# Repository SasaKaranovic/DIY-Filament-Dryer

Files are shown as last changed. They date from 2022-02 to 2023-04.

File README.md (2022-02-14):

# DIY WiFi Enabled 3D Printing Filament Dry Box

## What is this project about?
DIY WiFi Enabled Filament Dry Box (http://www.youtube.com/watch?v=txF2oQPIjb4 "DIY WiFi Enabled Filament Dry Box")

Above video shows the finished DryBox, how it works and motivation behind some of the design decisions.

## How can I build my own?
The above video explains the idea and how hardware and firmware works. It's recommended that you watch that first.
Hardware and firmware build instructions and source files are available in their respective folders.

---

Blog page: https://sasakaranovic.com/projects/diy-filament-dry-box

YouTube video: http://www.youtube.com/watch?v=txF2oQPIjb4

---

#### Sasa Karanovic

<a href="https://sasakaranovic.com/" target="_blank" title="Sasa Karanovic Home Page"> Home Page</a> &nbsp;&middot;&nbsp;
<a href="https://youtube.com/c/sasakaranovic" target="_blank" title="Sasa Karanovic on YouTube"> YouTube</a> &nbsp;&middot;&nbsp;
<a href="https://github.com/sasakaranovic" target="_blank" title="Sasa Karanovic on GitHub"> GitHub</a> &nbsp;&middot;&nbsp;
<a href="https://twitter.com/_sasakaranovic_" target="_blank" title="Sasa Karanovic on Twitter"> Twitter</a> &nbsp;&middot;&nbsp;
<a href="https://instagram.com/_sasakaranovic_" target="_blank" title="Sasa Karanovic on Instagram"> Instagram</a> &nbsp;&middot;&nbsp;
<a href="https://buymeacoffee.com/sasakaranovic" target="_blank" title="Sasa Karanovic on Buy me a coffee"> Buy me a coffee</a>

[home]: https://raw.githubusercontent.com/SasaKaranovic/common/master/assets/img_home.png "Sasa Karanovic Home Page"
[youtube]: https://raw.githubusercontent.com/SasaKaranovic/common/master/assets/img_youtube.png "Sasa Karanovic YouTube channel"
[github]: https://raw.githubusercontent.com/SasaKaranovic/common/master/assets/img_github.png "Sasa Karanovic on GitHub"
[twitter]: https://raw.githubusercontent.com/SasaKaranovic/common/master/assets/img_twitter.png "Sasa Karanovic on Twitter"
[instagram]: https://raw.githubusercontent.com/SasaKaranovic/common/master/assets/img_instagram.png "Sasa Karanovic on Instagram"
[coffee]: https://raw.githubusercontent.com/SasaKaranovic/common/master/assets/img_coffee.png "Buy me a coffee"

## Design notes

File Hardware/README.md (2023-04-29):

# Building the Hardware

### Schematic
Schematic files are available in `Schematic.pdf` as well as Altium source files.
This file should be enough to understand how things are connected and how hardware works.

Bill of Material is available in `Bill of Materials.pdf`.
Most parts are interchangeable, so feel free to source these parts from your favorite part distributor.
When replacing capacitors, make sure you choose the same voltage rating!

### How can I order the PCB

I have prepared Gerber files that are verified and ready to go. You can take `Release\2023-04-29_14-32_DryBox_R1\2023-04-29_14-32_DryBox_R1_Gerber.zip` and upload it to your favorite PCB manufactuer like PCBWay, SeeedStudio, JLCPCB etc.
There are no critical PCB specs, so you can select whichever one you prefer.
For your reference, the specifications for the PCBs that I have ordered are listed below.

PCB Specs:
- Board type: Single pieces
- Different Design in Panel：1
- Layer: 2 Layers
- Thickness: 1.6 mm
- Min Track/Spacing: 6/6mil
- Material: FR-4: TG150
- Min Hole Size: 0.3mm ↑
- Solder Mask: White
- Silkscreen: Black
- Quantity: 10 (or however many you need)
- Edge connector: No
- Surface Finish: HASL lead free (or ENIG but it's more expensive)
- "HASL" to "ENIG"  Yes
- Via Process: Tenting vias
- Finished Copper: 1 oz Cu

## Changelog

### 2023-04-29

- Corrected U3 part number

### 2021-12-07

- Initial release

[<- Go back to repository root](../README.md)

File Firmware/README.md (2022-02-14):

# How to build firmware

For our firmware development, we are going to use Arduino. Mainly because it's user friendly, easy to use and
most hobbyists are familiar with it or have already used it. While we could build te same or even more efficient
firmware using C and ESP-IDF, we are going to stick with Arduino and hope that this allows the project to be
more friendly and easier to use/modify by wider DIY/hacker community.

## How can I build/compile firmware?
Arduino has many third party libraries that you can use and also build firmware for many different boards.
However, depending for which board you are building firmware and also which libraries your project (sketch) uses,
you might need to manually install them or download them trough board/library manager.

While above mentioned solution works fine, it can lead to issues like installing the "wrong/different" version
of the library, different board files, "wrong/different" build/upload tools and so on. On top of that, since board files
and libraries are shared, we could install a library or a board file while working on another project that breaks our current project.
Hopefully you can see why this is not so great for open-source open-hardware project where we want everyone to be able to easily
checkout a repository and hit the ground running without spending hours setting up and debugging what library or board files are missing.

Luckily we can automate/avoid this by using a build system like PlatformIO. So below we will have two ways of building
the firmware, one will be "easy" by leveraging PlatformiIO build system, and the other one will be a manual one by using
Arduino IDE and manually searching and downloading all the board/library files.

## - The super easy way - Compile and upload using PlatformIO build system  - 

### 1. Install PlatformIO
Installing PlatformIO CLI is pretty straight-forward and also well documented for Windows, Linux and MacOS.
You will need to follow few steps and get PlatformIO CLI installed, detailed tutorial can be found at https://platformio.org/install/cli
Make sure to install [PlatformIO Core](https://docs.platformio.org/en/latest//core/installation.html#installation-methods 'https://docs.platformio.org/en/latest//core/installation.html#installation-methods') and allso that it is available trough [shell](https://docs.platformio.org/en/latest//core/installation.html#piocore-install-shell-commands 'PlatformIO Core - Install Shell Commands¶').

### 2. Build firmware
Open shell/command-prompt and navigate to 'Firmware/platformio' folder.
1. Compile the firmware by typing `pio run`, PlatformIO will download all the required board files and libraries and finally compile the firmware.
2. Upload the firmware with `pio run --target upload --upload-port <COM-PORT>`. Make sure to replace `<COM-PORT>` with your ESP32's COM port (ie COM1 or /dev/ttyACM0)
3. Upload the file system (Web page) with `pio run --target uploadfs --upload-port <COM-PORT>`, again replace `<COM-PORT>` with your ESP32's COM port.

Every time you make a firmware change, you need to run steps #1 and #2.
Every time you make a change to the web page (anything inside `data` folder) you only need to run step #3.

## - The less easy way - Compile using Arduino IDE and manually install all board files and libraries

### 1. Install Arduino IDE
Download and install Arduino IDE from https://www.arduino.cc/en/software

### 2. Install ESP32 board files
Add ESP32 board files to you Arduino IDE
1. Go to `File -> Preferences`
2. Find `Additional Board Manager URLs:` and add `https://dl.espressif.com/dl/package_esp32_index.json`
3. Go to `Boards -> Board manager`.
4. Search for `esp32`.
5. Find a board package title `esp32 -> by Espressif Systems` and install it.
(Currently we are using version 1.0.6, in case you have any issues, try installing this exact version)

### 3. Install libraries used by the project
Install third party libraries that required
1. Go to `Sketch -> Include Library -> Manage Libraries... (CTRL+SHIFT+I)`
2. Find libraries from the list below and install them one by one

- Adafruit SHT31 Library (version 2.0.0)
- Adafruit Si7021 Library (version 1.5.0)
- DallasTemperature (version 3.9.0)
- OneWire (version 2.3.6)

### 4. Install some more libraries
You will manually have to install following libraries.
One way is to create a `Libraries` folder in your sketch folder. Then download the libraries and place them in Libraries folder.

- https://github.com/me-no-dev/AsyncTCP
- https://github.com/me-no-dev/ESPAsyncWebServer

### 5. Select build board
You need to tell Arduino IDE for which board we want to build the firmware.
Go to `Tools -> Board: -> ESP32 Arduino` and select `ESP32 Dev Module`
Go to `Tools -> Port` and select your ESP32 COM port

### 6. Compile and upload the firmware
You need to compile and upload firmware.
Go to `Sketch -> Upload`
You will need to do this step every time you make a change to the firmware.

### 7. Upload the file system
You need to tell Arduino IDE which partition scheme we want to use
Go to `Tools -> Partition Scheme` and select `1MB APP / 3MB SPIFF`
Now you can go upload file system trough `Tools -> ESP32 Sketch Data Upload` menu item.
If you are missing above menu item, you will need to manually install [ESP32 Sketch Data Upload tool](https://github.com/me-no-dev/arduino-esp32fs-plugin).
You will need to do this step every time you make a change to the web page (or anything inside the data folder)

[<- Go back to repository root](../README.md)

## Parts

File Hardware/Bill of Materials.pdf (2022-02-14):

Designator | Description | Distributor | Distributor Part Number | Manufacturer | Manufacturer Part Number | Quantity
C1, C6, C15, C22 | Capacitor | DigiKey | 1276-1870-1-ND | Samsung Electro-Mechanics | CL10A106MO8NQNC | 4
C2, C4, C8, C9, C11, C13, C14, C21 | Capacitor | DigiKey | 1276-1009-1-ND | Samsung Electro-Mechanics | CL10B103KB8NNNC | 8
C3, C10 | Polarized Capacitor (Axial) | DigiKey | 732-9599-1-ND | Würth Elektronik | 860160674021 | 2
C5, C7, C12, C20 | Capacitor | DigiKey | 1276-1860-1-ND | Samsung Electro-Mechanics | CL10A105KB8NNNC | 4
D1 | Red, Green, Blue (RGB) - LED Indication - Discrete 1.9V Red, 2.8V Green, 2.8V Blue 0606 (1616 Metric) | DigiKey | 1080-1551-1-ND | Everlight Electronics Co Ltd | EAST1616RGBB2 | 1
D2, D3, D4 | | DigiKey | 1727-3848-1-ND | Nexperia USA Inc. | PMEG6010CEH,115 | 3
F1 | Thermal Fuse | DigiKey | SF-1206SP200-2CT-ND | Bourns Inc. | SF-1206SP200-2 | 1
L1 | Inductor | DigiKey | 445-180842-1-ND | TDK Corporation | VLS6045AF-101M | 1
P1, P2, P3, P4, P5, P8, P11 | Header, 4-Pin, Header, 3-Pin, Dual row, Header, 2-Pin, Header, 3-Pin | | | | | 7
Q1, Q3 | MOSFET N-CH 60V 0.38A | DigiKey | DMN62D0U-13DICT-ND | Diodes Incorporated | DMN62D0U-13 | 2
Q2 | MOSFET N-CH 30V 37A LFPAK | DigiKey | | Nexperia USA Inc. | PSMN011-30YLC,115 | 1
R1, R11 | Resistor | DigiKey | RMCF0603JT2K20CT-ND | Stackpole Electronics Inc | RMCF0603JT2K20 | 2
R2, R3, R10 | Resistor | DigiKey | RMCF0603FT220RCT-ND | Stackpole Electronics Inc | RMCF0603FT220R | 3
R5, R18, R23 | Resistor | DigiKey | RMCF0603JT10K0CT-ND | Stackpole Electronics Inc | RMCF0603JT10K0 | 3
R6, R7, R8, R9, R12 | Resistor | DigiKey | RMCF0603FT4K70CT-ND | Stackpole Electronics Inc | RMCF0603FT4K70 | 5
R13, R17, R22 | Resistor | DigiKey | RMCF0603FT100RCT-ND | Stackpole Electronics Inc | RMCF0603FT100R | 3
R19 | Resistor | DigiKey | RNCS0603BKE1K00CT-ND | Stackpole Electronics Inc | RNCS0603BKE1K00 | 1
R20 | Resistor | DigiKey | RMCF0603ZT0R00CT-ND | Stackpole Electronics Inc | RMCF0603ZT0R00 | 1
SW1 | SWITCH TACTILE SPST-NO 0.05A 12V | DigiKey | CKN9088CT-ND | C&K | PTS645SL50SMTR92 LFS | 1
U1 | | | | Espressif Systems | ESP32-WROOM-32D (4MB HIGH TEMP) | 1
U2 | Switching mode regulator [ 3v3, 5v, 12v and ADJ ] | DigiKey | LM2576S-5.0/NOPB-ND | Texas Instruments | LM2576S-5.0/NOPB | 1
U3 | High-Performance Single 1.8V@150mA LDO | DigiKey | 576-4082-1-ND | Microchip Technology | MIC5365-1.8YD5-TR | 1

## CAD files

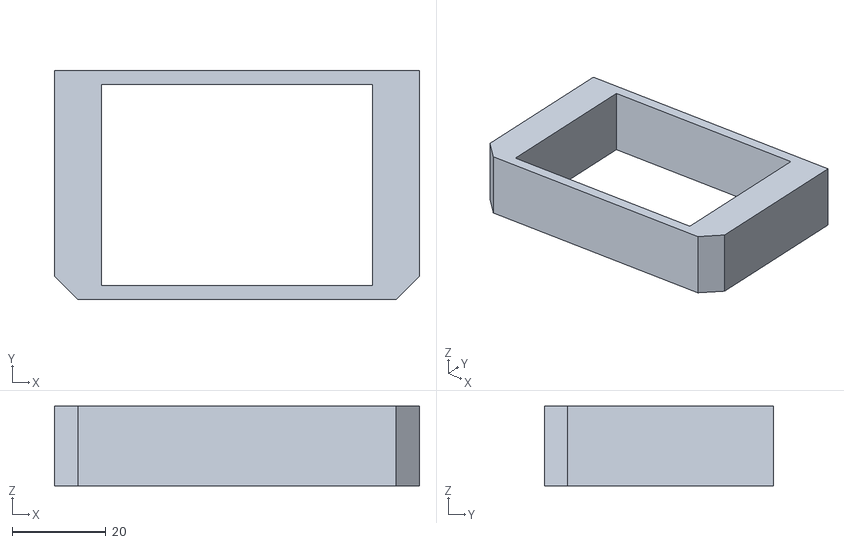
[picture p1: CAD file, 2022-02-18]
3D_Parts/Rubber_Friction_Mount_TPU.stl
78.0 x 49.0 x 17.0

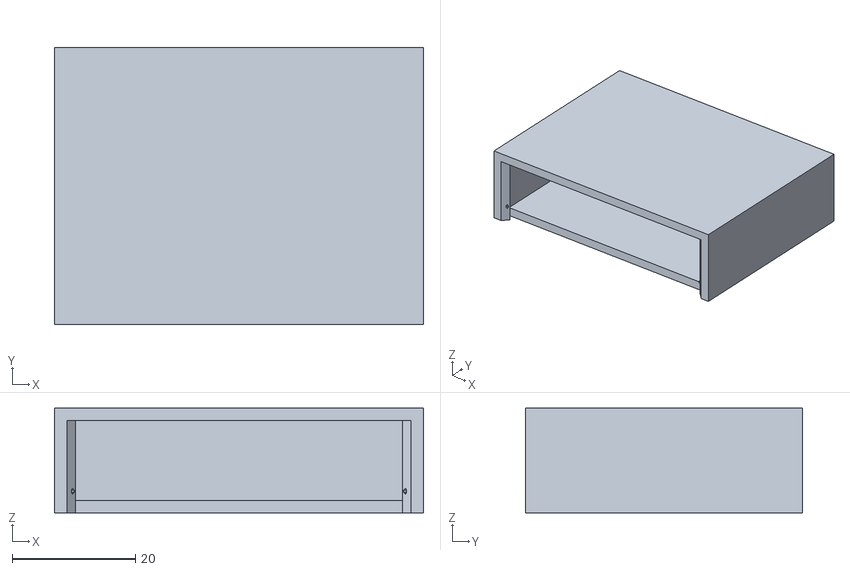
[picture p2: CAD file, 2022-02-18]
3D_Parts/Desiccant_Holder_PLA_or_PETG.stl
60.0 x 45.0 x 17.0

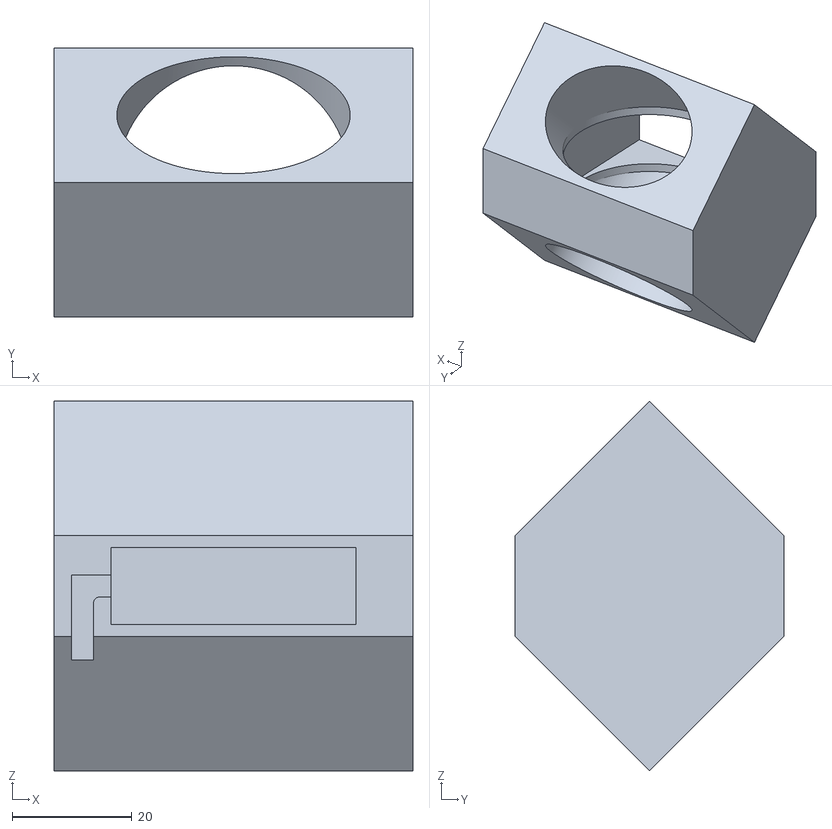
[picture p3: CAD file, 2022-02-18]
3D_Parts/FanHolder_PLA_or_PETG.stl
60.0 x 45.0 x 61.8

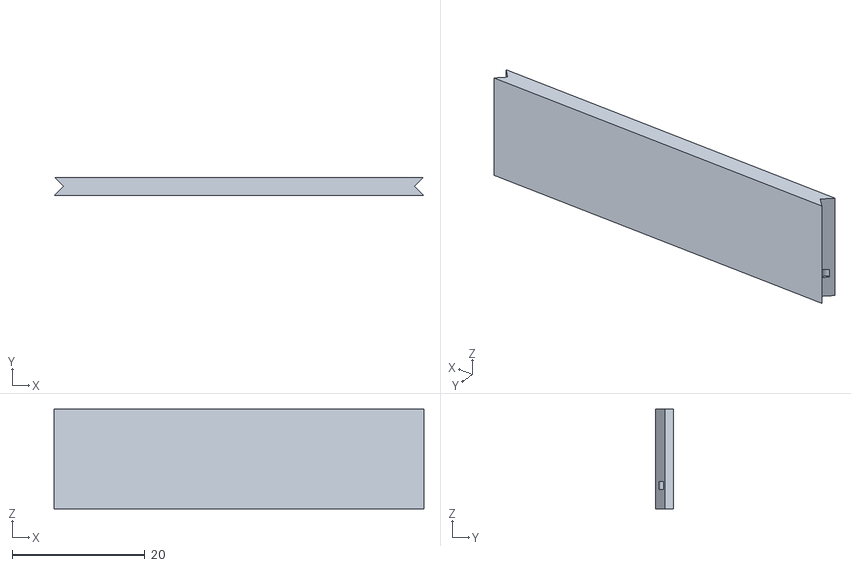
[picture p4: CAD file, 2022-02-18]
3D_Parts/Desiccant_Cap_PLA_or_PETG.stl
55.7 x 2.73 x 15.0

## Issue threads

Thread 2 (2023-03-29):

BOM Parts.

SilentStray, 2023-03-29:
Header Part Numbers:
P2 | Connector   Header Through Hole 6 position 0.100" (2.54mm) | DigiKey | S2011EC-03-ND | Sullins   Connector Solutions | PRPC003DAAN-RC | Quantity - 1

P3,P8 | Connector   Header Through Hole 2 position 0.100" (2.54mm) | DigiKey | S1011EC-02-ND | Sullins   Connector Solutions | PRPC002SAAN-RC | Quantity - 2

P1,P4,P11 | Connector   Header Through Hole 4 position 0.100" (2.54mm) | DigiKey | S1011EC-04-ND | Sullins   Connector Solutions | PRPC004SAAN-RC | Quantity - 3

P5 | Connector   Header Through Hole 3 position 0.100" (2.54mm) | DigiKey | S1011EC-03-ND | Sullins   Connector Solutions | PRPC003SAAN-RC | Quantity - 1

L1 is out of stock on DigiKey:

L1 | Inductor | Mouser | 810-VLS6045AF-101M | TDK Corporation | VLS6045AF-101M |  Quantity - 1

SilentStray, 2023-03-30:
Made a pull request.

Closed 2023-03-30.

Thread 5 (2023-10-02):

PID values when 'Using HEATER as target temperature' returning negative

benuron, 2023-10-02:
Hi Sasa, thanks for sharing this project and make it available to everyone :)

I am trying to setup the whole project since a while now, I am not a code expert so my efforts to fix some bugs are reaching a limit.

One situation that is that when the max_heater_temperature reaches the set value the PID values starts to get negative and the calculated PWM values shoot to the max and the heater keeps ON.

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

Am I missing something?
I am trying to create a branch and contribute for this project as soon as I understand git better 👍

SasaKaranovic, 2024-02-29:
@benuron appologies for late reply. I somehow missed that you have opened this issue.

Did you modify the code or using it as-is?

I am working on a new version of this project that should hopefully be better and offer some quality of life improvements.

benuron, 2024-03-03:
@SasaKaranovic thanks for replying!

I am using some slightly modified code but nothing regarding the PID. In my code I changed the wifi connection, and I am using two SHT31 ```
Adafruit_SHT31 temp_sensor_in = Adafruit_SHT31();
Adafruit_Si7021 temp_sensor_out = Adafruit_SHT31();
```
and in this section I modified the i2c address in the temp_sensor_out

```
 // Setup temperature and humidity oneWireSensors
    if (!temp_sensor_out.begin(0x45))
    {
        Serial.println("Can't find Si7021 sensor! (out sensor)");
        LED_ALL_OFF();
        while (1)
        {
            LED_ON(PIN_LED_BLUE);
            delay(250);
            LED_OFF(PIN_LED_BLUE);
            delay(250);
        }
    }

    Wire.setClock(10000);
    if (!temp_sensor_in.begin(0x44))
    {
        Serial.println("Can't find SHT31! (in sensor)");
        LED_ALL_OFF();
        while (1)
        {
            LED_ON(PIN_LED_GREEN);
            delay(250);
            LED_OFF(PIN_LED_GREEN);
            delay(250);
        }
    }   if (!temp_sensor_out.begin())
    {
        Serial.println("Can't find Si7021 sensor! (out sensor)");
        LED_ALL_OFF();
        while (1)
        {
            LED_ON(PIN_LED_BLUE);
            delay(250);
            LED_OFF(PIN_LED_BLUE);
            delay(250);
        }
    }

    Wire.setClock(10000);
    if (!temp_sensor_in.begin(0x44))
    {
        Serial.println("Can't find SHT31! (in sensor)");
        LED_ALL_OFF();
        while (1)
        {
            LED_ON(PIN_LED_GREEN);
            delay(250);
            LED_OFF(PIN_LED_GREEN);
            delay(250);
        }
    }
```
From the webUI, all values are good, just the strange behaviour with the PID. I tried to manually tweak them a bit but without much success. Would be possible to have a PID autotune feature like in Marlin firmware?

There is a difference in hardware from my S1 (I have five) to yours. They all run with 24V power supplies. With the BOM for 12V the MOSFET generates a bunch of heat. I had to recalculate the voltage divider values so the MOSFET is full on/off.

Would love to try the new version, thank you for the efforts!

SasaKaranovic, 2024-06-05:
Closing due to inactivity. We can pick it up if new information becomes available.

razserv2010, 2024-08-01:
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

Hi SasaKaranovic
Is there already a new version?

Closed 2024-06-05.

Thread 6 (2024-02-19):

A fatal error occurred: Failed to connect to ESP32: No serial data received.

razserv2010, 2024-02-19:
I'm experiencing a error:
A fatal error occurred: Failed to connect to ESP32: No serial data received.
I connected using FTDI232
3V3 - 3V3
TX - RX
RX - TX
GND - GND

Could it be that the U3 component is MIC5365-1.8YD5-TR instead of 3V3?

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

SasaKaranovic, 2024-02-19:
Hi Raz,

Sorry about that, there was a typo in the BoM but it's fixed now.
You would need `MIC5365-3.3YD5-TR` (or any other equivalent 3v3 LDO).

razserv2010, 2024-02-19:
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

So this is the reason why the pc does not recognize the esp32?

SasaKaranovic, 2024-02-19:
Yes. The regulator you are using is providing ESP32 with 1.8V which is not enough for it to power up.
If you switch to a 3.3V regulator, it should work (assuming everything else is ok).

razserv2010, 2024-02-19:
> Yes. The regulator you are using is providing ESP32 with 1.8V which is not enough for it to power up.
> If you switch to a 3.3V regulator, it should work (assuming everything else is ok).

Thanks, I ordered 3v

SasaKaranovic, 2024-02-19:
Sorry about that. The release files and the Altium files were updated a long time ago but when you mentioned it, I realized that the schematic is still calling out the wrong LDO.

razserv2010, 2024-02-19:
> Sorry about that. The release files and the Altium files were updated a long time ago but when you mentioned it, I realized that the schematic is still calling out the wrong LDO.

Sorry but I didn't understand, LDO?

SasaKaranovic, 2024-02-20:
[LDO regulator](https://en.wikipedia.org/wiki/Low-dropout_regulator).
The schematic had the wrong LDO part number. If you replace it with 3.3V regulator, it should work.

razserv2010, 2024-02-20:
> [LDO regulator](https://en.wikipedia.org/wiki/Low-dropout_regulator).
> The schematic had the wrong LDO part number. If you replace it with 3.3V regulator, it should work.

Thanks, I ordered 3.3V

razserv2010, 2024-02-25:
> [LDO regulator](https://en.wikipedia.org/wiki/Low-dropout_regulator). The schematic had the wrong LDO part number. If you replace it with 3.3V regulator, it should work.

I replaced the component but still:
A fatal error occurred: Failed to connect to ESP32: No serial data received.

What is the order of UART connections? , maybe I didn't connect correctly..

razserv2010, 2024-02-26:
> [LDO regulator](https://en.wikipedia.org/wiki/Low-dropout_regulator).
> The schematic had the wrong LDO part number. If you replace it with 3.3V regulator, it should work.

 After I replaced the component, I was able to upload the firmware but the esp32 does not connect to wifi

razserv2010, 2024-02-26:
Until the Si7021 sensors arrive, I want to connect the board but it won't let me connect to wifi
How can Si7021 be bypassed?

katodo, 2024-02-27:
you can start to bypass "if (!temp_sensor_out.begin())" at the begin of code.

SasaKaranovic, 2024-02-29:
@razserv2010 As @katodo said you could stub out (comment out) parts of the code that rely on Si7021.
But it might be tedious and also I would recommend using the sensor since some portions of the code depend on it.

I am working on new version of this board that should offer some improvements that people have asked for.

razserv2010, 2024-03-01:
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

The sensors arrived, trying to connect to wifi but without success, I opened a new issue about it.

Closed 2024-03-02.

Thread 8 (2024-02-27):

(R4) component Also missing is the Bill of Materials

razserv2010, 2024-02-27:
I noticed that the R4 component is missing, Could you please provide the name of the component needed?
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

SasaKaranovic, 2024-02-29:
R4 is marked as DNP (do not populate or do not purchase). So you are correct not to populate it on the board.

This is a fallback if you are using an adjustable voltage regulator in which case you would change the value of R20 and R4.

Closed 2024-02-29.

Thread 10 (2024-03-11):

Custom Board: Can't connect to WiFi

razserv2010, 2024-03-11:
My board only manages to connect to wifi if the UART flasher is also connected, if I disconnect the UART and leave only the main power connected then the wifi does not connect.
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

SasaKaranovic, 2024-06-05:
Closing due to inactivity. We can pick it up if new information becomes available.

Closed 2024-06-05.

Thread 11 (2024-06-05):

errors in compile wiith platformio

Motarbio, 2024-06-05:
compiling aborted with this errors

> pio run
Processing esp32dev (framework: arduino; platform: espressif32; board: esp32dev)
---------------------------------------------------------------------------------------------------
Verbose mode can be enabled via `-v, --verbose` option
CONFIGURATION: https://docs.platformio.org/page/boards/espressif32/esp32dev.html
PLATFORM: Espressif 32 (6.7.0) > Espressif ESP32 Dev Module
HARDWARE: ESP32 240MHz, 320KB RAM, 4MB Flash
DEBUG: Current (cmsis-dap) External (cmsis-dap, esp-bridge, esp-prog, iot-bus-jtag, jlink, minimodule, olimex-arm-usb-ocd, olimex-arm-usb-ocd-h, olimex-arm-usb-tiny-h, olimex-jtag-tiny, tumpa)
PACKAGES:
 - framework-arduinoespressif32 @ 3.20016.0 (2.0.16)
 - tool-esptoolpy @ 1.40501.0 (4.5.1)
 - tool-openocd-esp32 @ 2.1100.20220706 (11.0)
 - toolchain-xtensa-esp32 @ 8.4.0+2021r2-patch5
Converting src.ino
LDF: Library Dependency Finder -> https://bit.ly/configure-pio-ldf
LDF Modes: Finder ~ chain, Compatibility ~ soft
Found 40 compatible libraries
Scanning dependencies...
Dependency Graph
|-- SPI @ 2.0.0
|-- SPIFFS @ 2.0.0
|-- FS @ 2.0.0
|-- WiFi @ 2.0.0
|-- Adafruit SHT31 Library @ 2.2.2
|-- Adafruit Si7021 Library @ 1.5.3
|-- ESP Async WebServer @ 1.2.3
|-- AsyncTCP @ 1.1.1
|-- DallasTemperature @ 3.11.0
|-- OneWire @ 2.3.8
|-- ESPmDNS @ 2.0.0
|-- Wire @ 2.0.0
Building in release mode
Compiling .pio\build\esp32dev\src\src.ino.cpp.o
Linking .pio\build\esp32dev\firmware.elf
c:/users/magut/.platformio/packages/toolchain-xtensa-esp32/bin/../lib/gcc/xtensa-esp32-elf/8.4.0/../../../../xtensa-esp32-elf/bin/ld.exe: .pio\build\esp32dev\lib0ed\libESP Async WebServer.a(WebAuthentication.cpp.o):(.literal._ZL6getMD5PhtPc+0x4): undefined reference to `mbedtls_md5_starts'
c:/users/magut/.platformio/packages/toolchain-xtensa-esp32/bin/../lib/gcc/xtensa-esp32-elf/8.4.0/../../../../xtensa-esp32-elf/bin/ld.exe: .pio\build\esp32dev\lib0ed\libESP Async WebServer.a(WebAuthentication.cpp.o): in function `getMD5(unsigned char*, unsigned short, char*)':
C:\Users\Magut\Downloads\DIY-Filament-Dryer-master\DIY-Filament-Dryer-master\Firmware\platformio/.pio/libdeps/esp32dev/ESP Async WebServer/src/WebAuthentication.cpp:73: undefined reference to `mbedtls_md5_starts'
collect2.exe: error: ld returned 1 exit status
*** [.pio\build\esp32dev\firmware.elf] Error 1

SasaKaranovic, 2024-06-05:
Hey @Motarbio

From the output it looks like PlatformIO is identifying conflict between libraries.

Can you try updating `platformio.ini` file and changing lines Line 29 and Line 30 (https://github.com/SasaKaranovic/DIY-Filament-Dryer/blob/master/Firmware/platformio/platformio.ini#L29-L30) to be as follows

```
    https://github.com/me-no-dev/ESPAsyncWebServer.git
    https://github.com/me-no-dev/AsyncTCP.git
```

Motarbio, 2024-06-05:
Hi Now the error is please install  git clientDegiorgi Tiziano Il giorno 4 giu 2024, alle ore 22:02, Sasa Karanovic ***@***.***> ha scritto:
Hey @Motarbio
From the output it looks like PlatformIO is identifying conflict between libraries.
Can you try updating platformio.ini file and changing lines Line 29 and Line 30 (https://github.com/SasaKaranovic/DIY-Filament-Dryer/blob/master/Firmware/platformio/platformio.ini#L29-L30) to be as follows
    https://github.com/me-no-dev/ESPAsyncWebServer.git
    https://github.com/me-no-dev/AsyncTCP.git

—Reply to this email directly, view it on GitHub, or unsubscribe.You are receiving this because you were mentioned.Message ID: ***@***.***>

SasaKaranovic, 2024-06-05:
@Motarbio Can you try doing that?
You can install a Git client from https://git-scm.com/download/win (assuming you use Windows)

Motarbio, 2024-06-05:
Done, nothing dame errorDegiorgi Tiziano Il giorno 4 giu 2024, alle ore 23:08, Sasa Karanovic ***@***.***> ha scritto:
@Motarbio Can you try doing that?
You can install a Git client from https://git-scm.com/download/win (assuming you use Windows)

—Reply to this email directly, view it on GitHub, or unsubscribe.You are receiving this because you were mentioned.Message ID: ***@***.***>

SasaKaranovic, 2024-06-05:
Please try restarting your computer after installing Git client and then try again.

p.s. When you reply via email, it messes up the formatting on the GitHub issue.

Motarbio, 2024-06-05:
pc restarted, same error
Library Manager: Installing git+https://github.com/me-no-dev/ESPAsyncWebServer.git
UserSideException: Please install Git client from https://git-scm.com/downloads

Motarbio, 2024-06-05:
Hi there,
downloaded manually the libraries, compiled succesfully but with 2 warnings

Library Manager: Installing ESPAsyncWebServer-master
Warning! Could not find the package with 'ESPAsyncWebServer-master' requirements for your system 'windows_amd64'
Library Manager: Installing AsyncTCP-master
Warning! Could not find the package with 'AsyncTCP-master' requirements for your system 'windows_amd64'

SasaKaranovic, 2024-06-06:
You should double check if `git` is in your system `PATH` variable. Then PlatformIO should be able to pull those libraries for you automatically.

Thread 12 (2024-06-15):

ignores heater temp limit

gabecamp, 2024-06-15:
seems to ignore the heater temp limit and goes to 100c ,built as normal except for using 2 Adafruit SHT31 as in and out sensors,

SasaKaranovic, 2024-06-15:
@gabecamp Is the heater sensor reporting that temperature or you manually measured it?
Can you share which components you used and which PCB vendor?

gabecamp, 2024-06-16:
Using all the parts from the BOM on GitHub except for 2 sh31 sensors , the PCBs were using the Gerber's from github with jlcpcb. The temps are from the ds18b20 as per the schematic.  After some testing I found it does hold temp correctly after turning it off and letting it cool a few times. Could it possibly be the pid loop causing thermal runaway?

SasaKaranovic, 2024-06-17:
It's good that it's stable now.
I had mine running for couple of years now and had no issues.
If you find way to reproduce this, please let me know.

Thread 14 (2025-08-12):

PlatformIO build: FAILED

wigw, 2025-08-12:
Добрий день.
Даруйте мені, я не можу скомпілювати прошивку, пише FAILED.
Що я роблю не так

[FAILED.txt](https://github.com/user-attachments/files/21729861/FAILED.txt)

?

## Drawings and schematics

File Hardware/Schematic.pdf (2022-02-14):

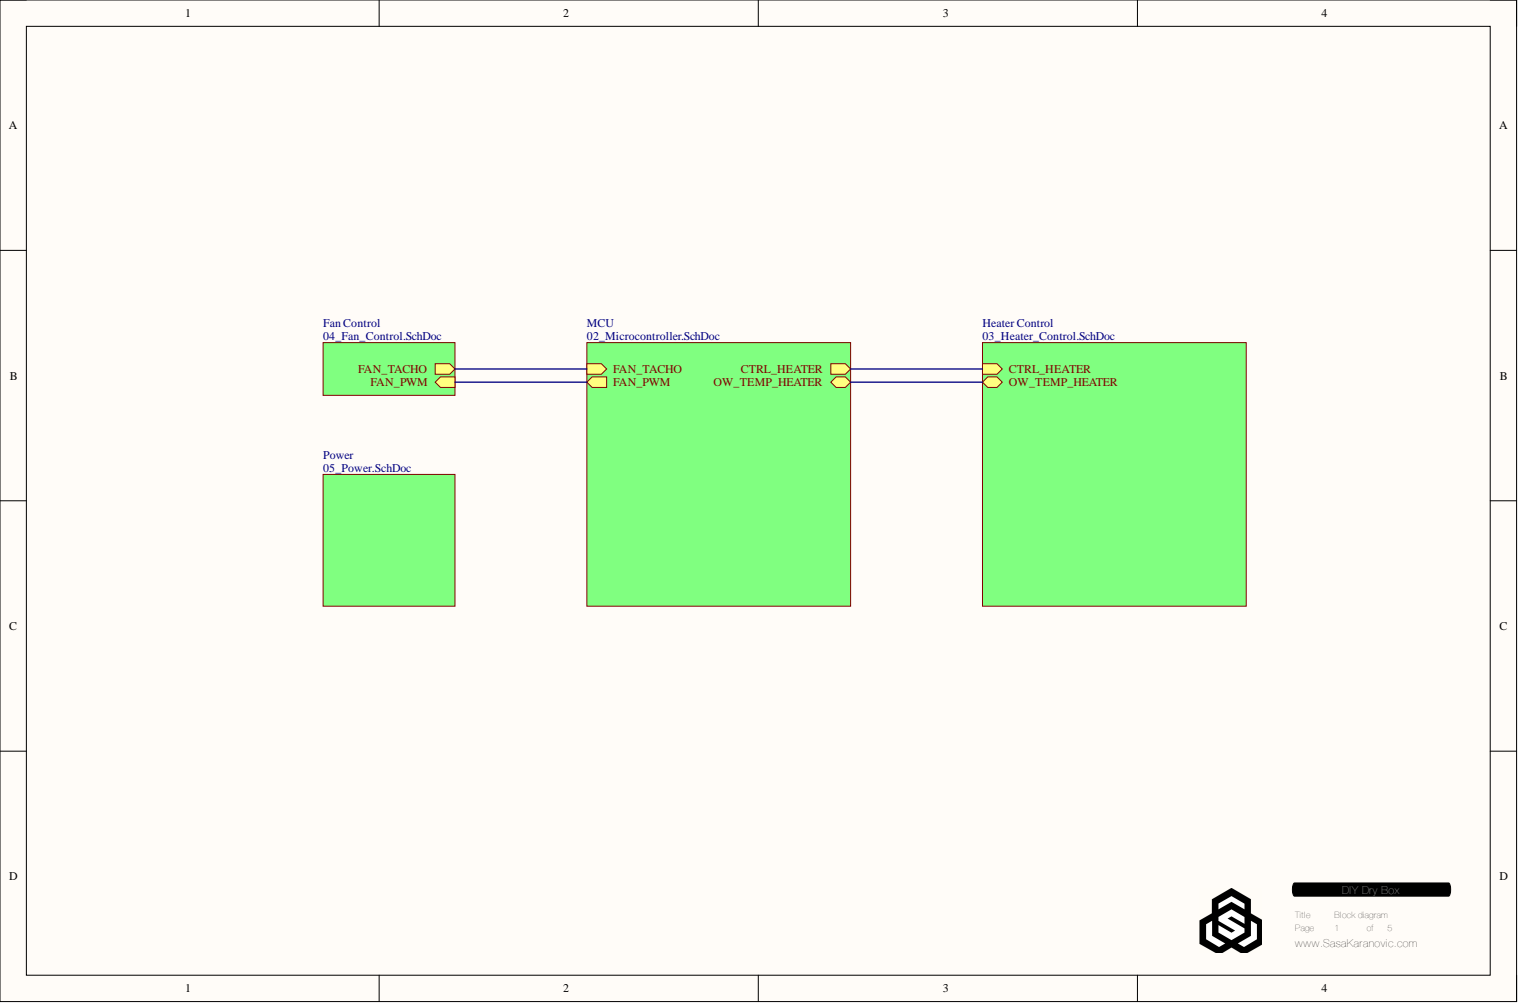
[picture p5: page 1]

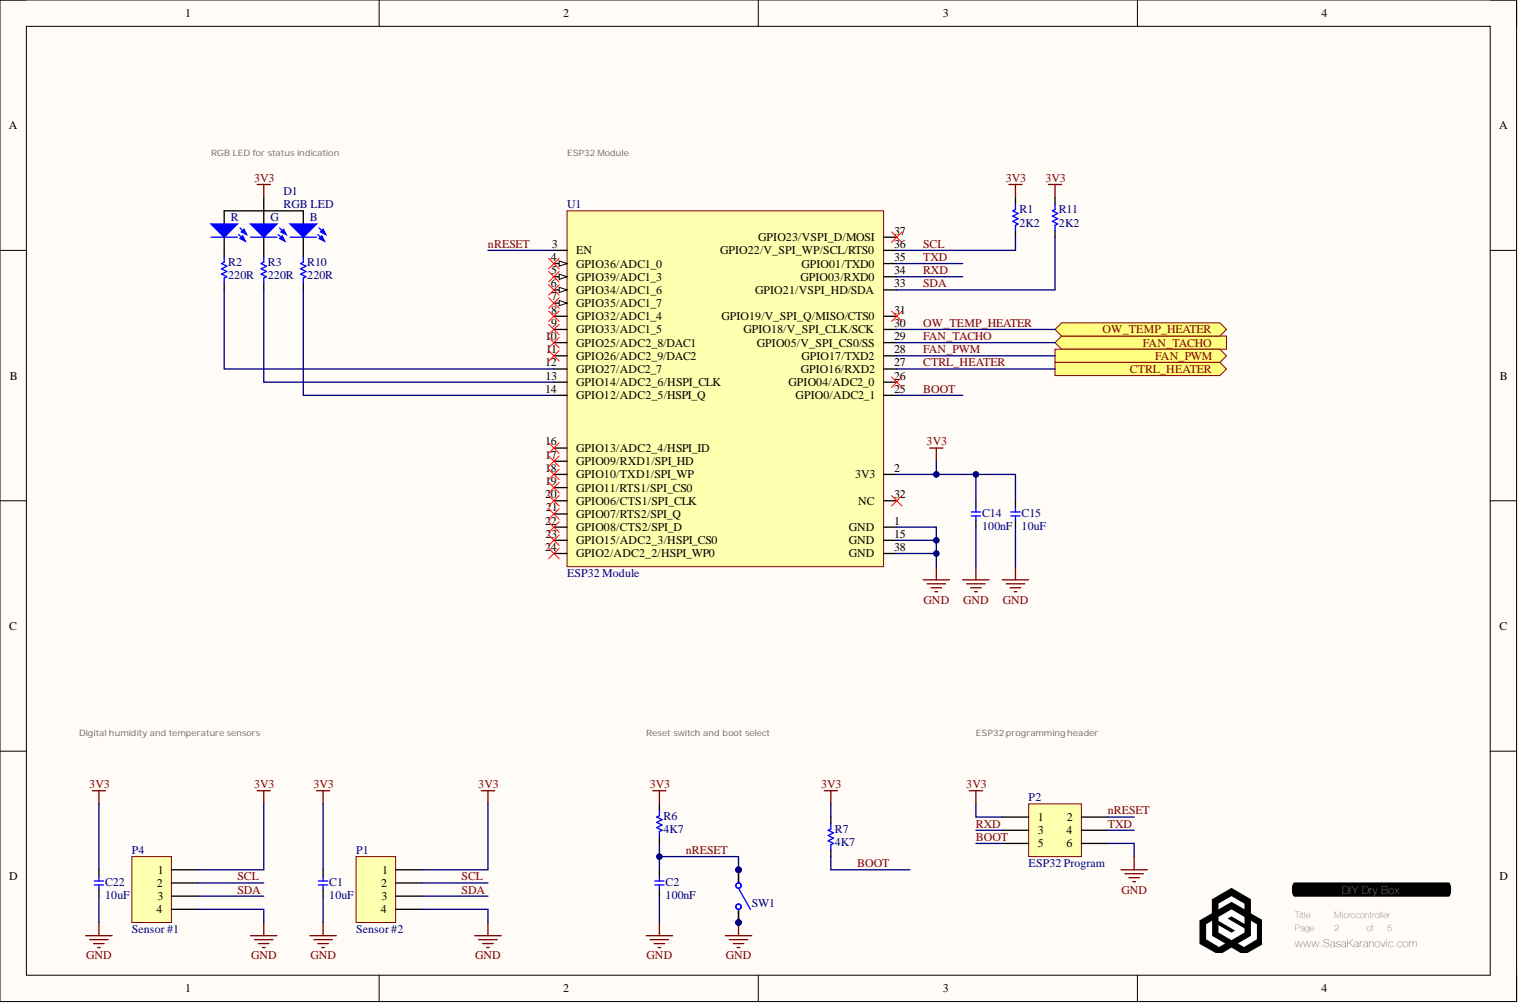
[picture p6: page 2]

SCL

GPIO36/ADC1_0 4 | | TXD RXD SDA

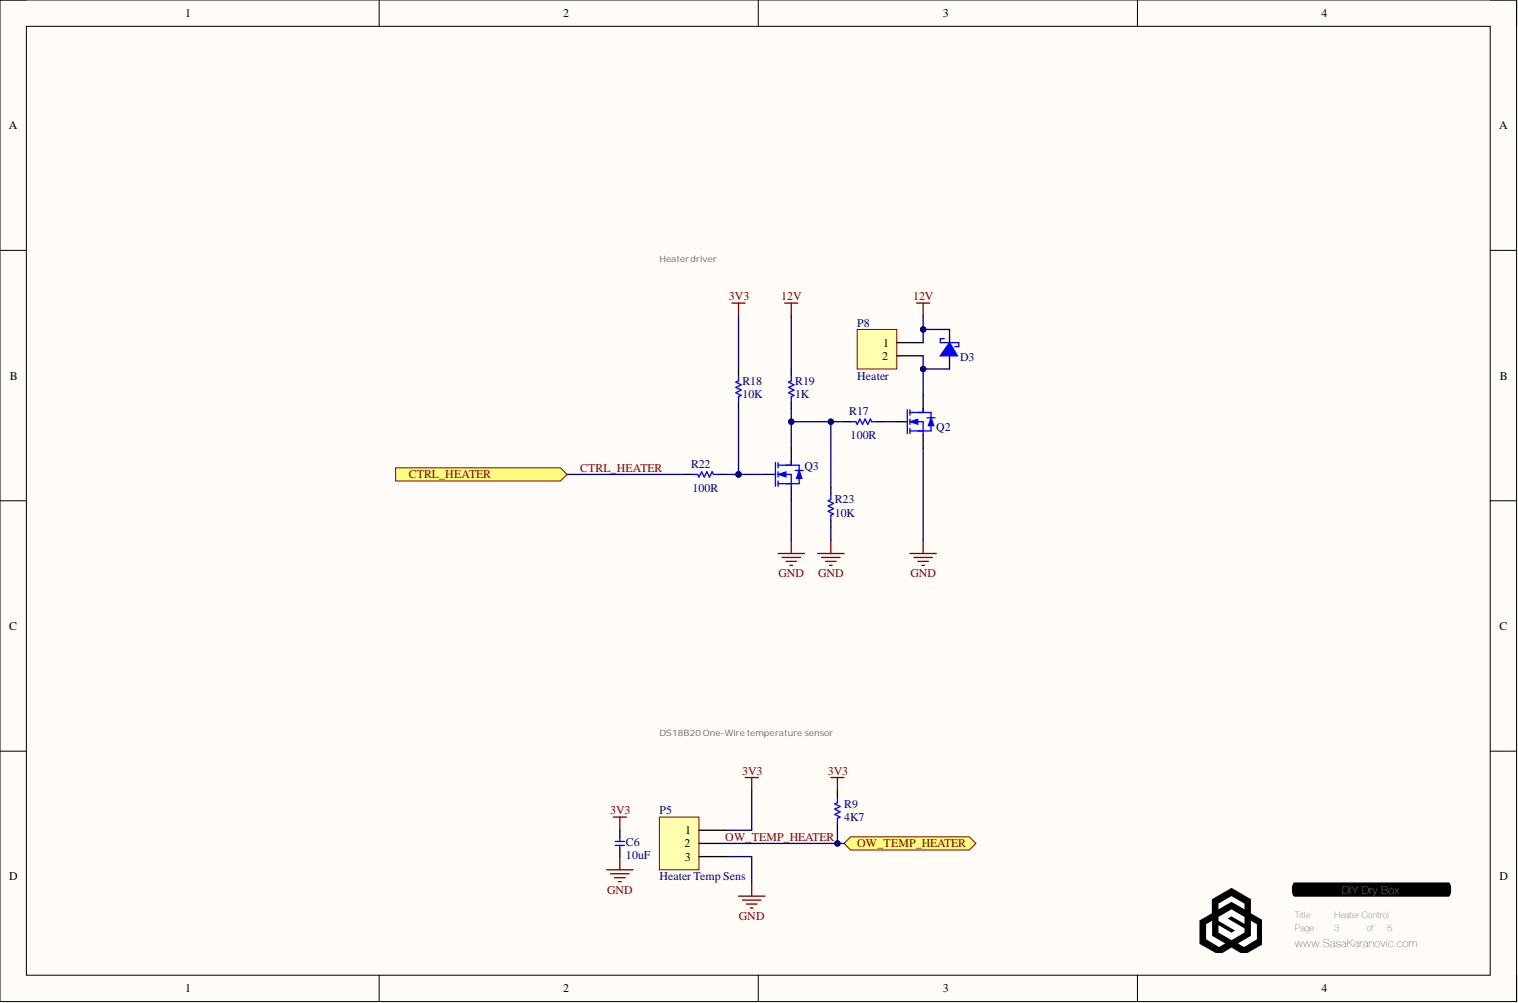
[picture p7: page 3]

DS18B20 One-Wire temperature sensor

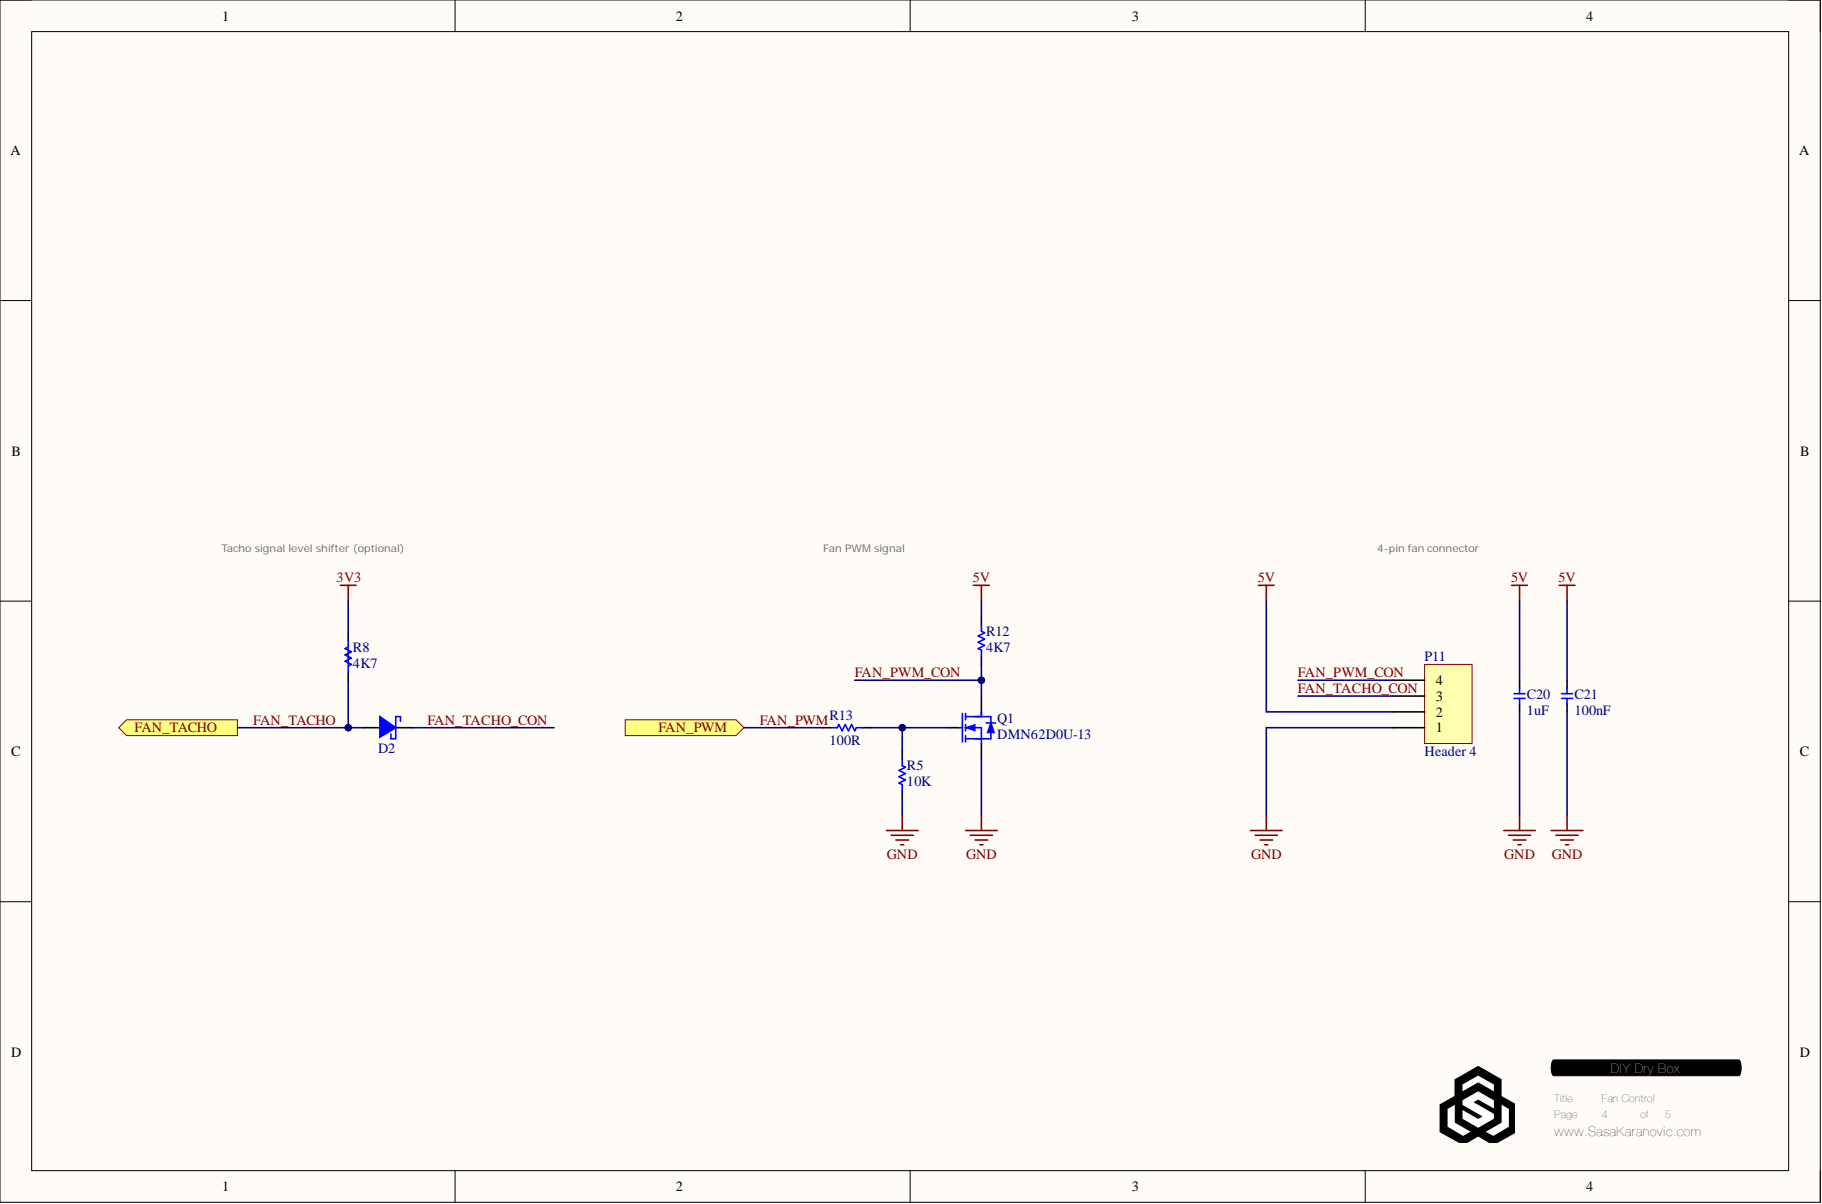
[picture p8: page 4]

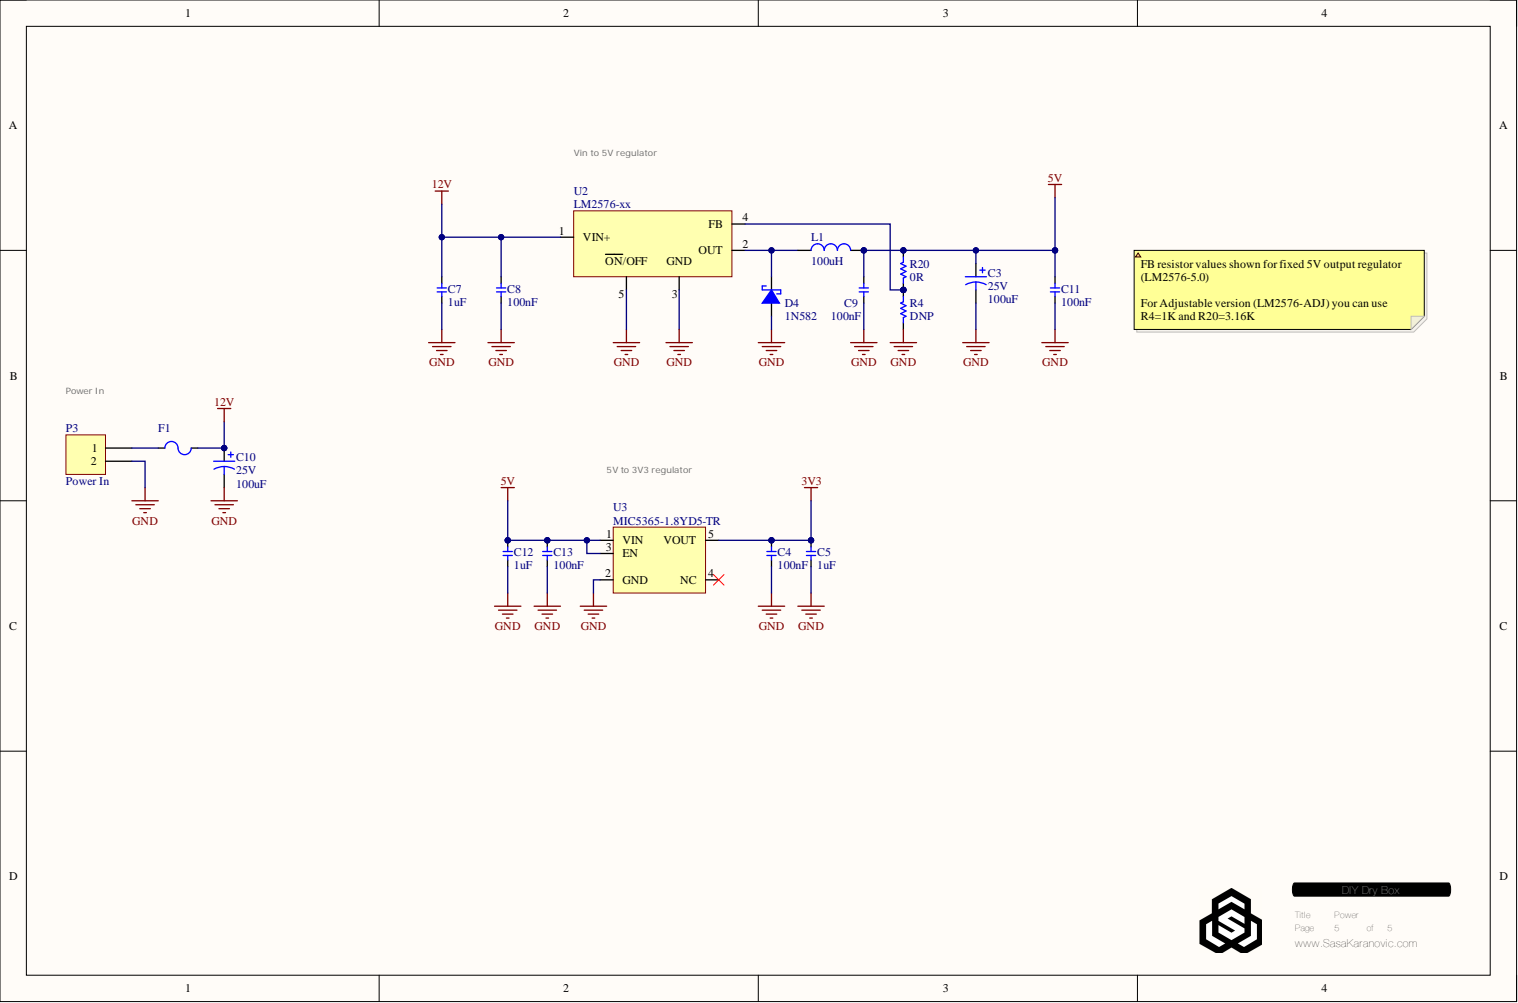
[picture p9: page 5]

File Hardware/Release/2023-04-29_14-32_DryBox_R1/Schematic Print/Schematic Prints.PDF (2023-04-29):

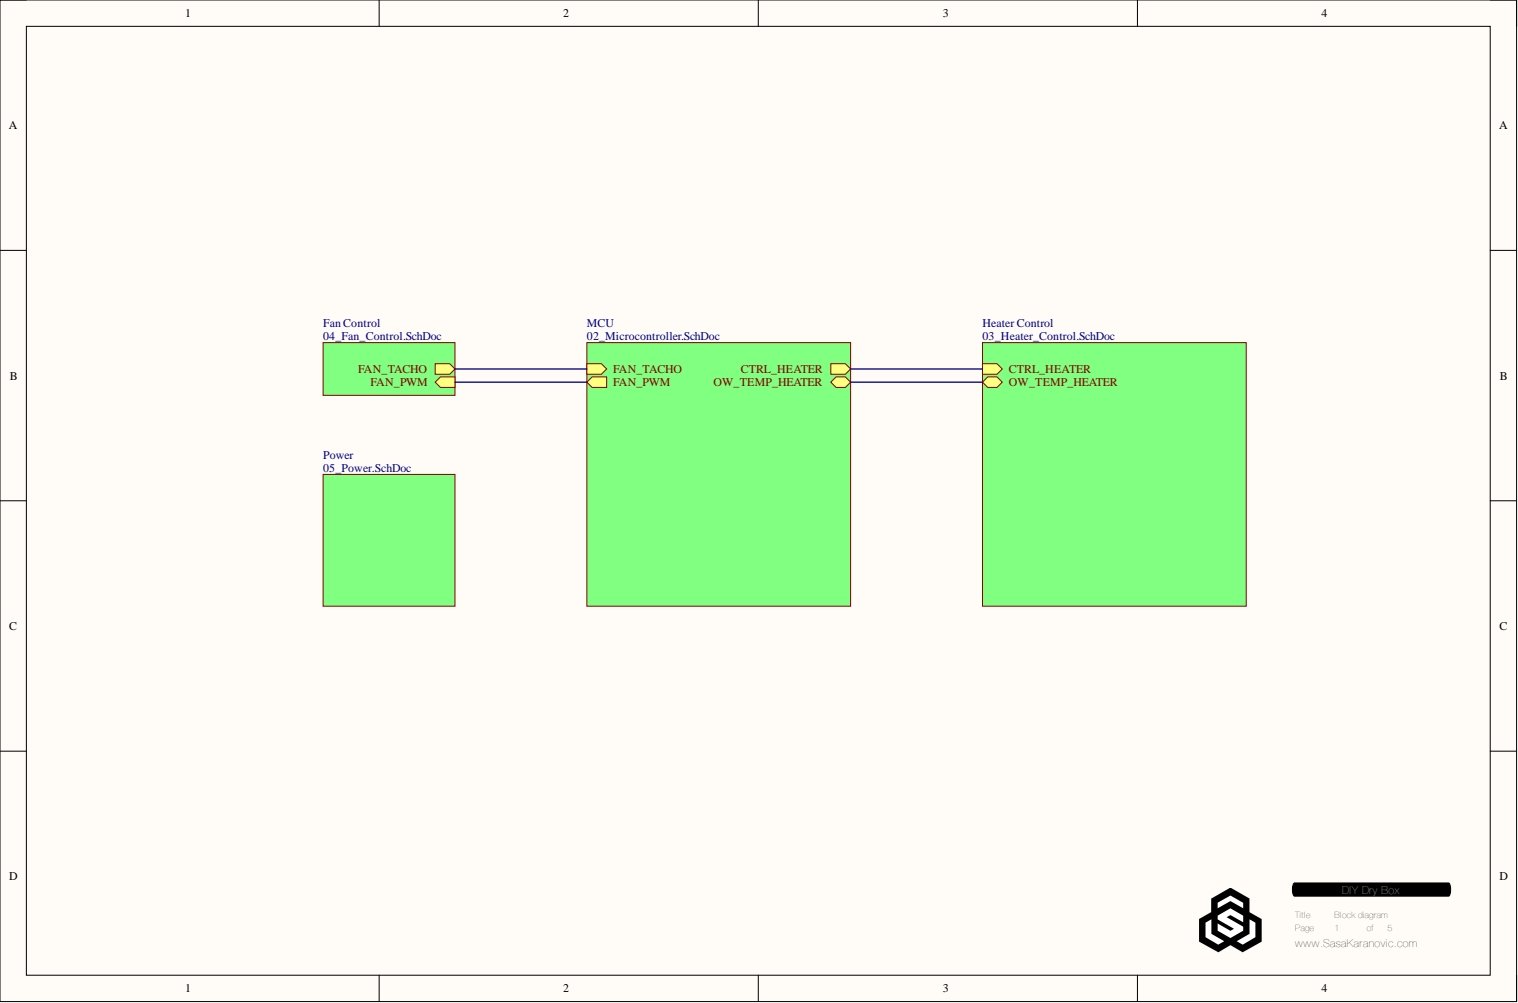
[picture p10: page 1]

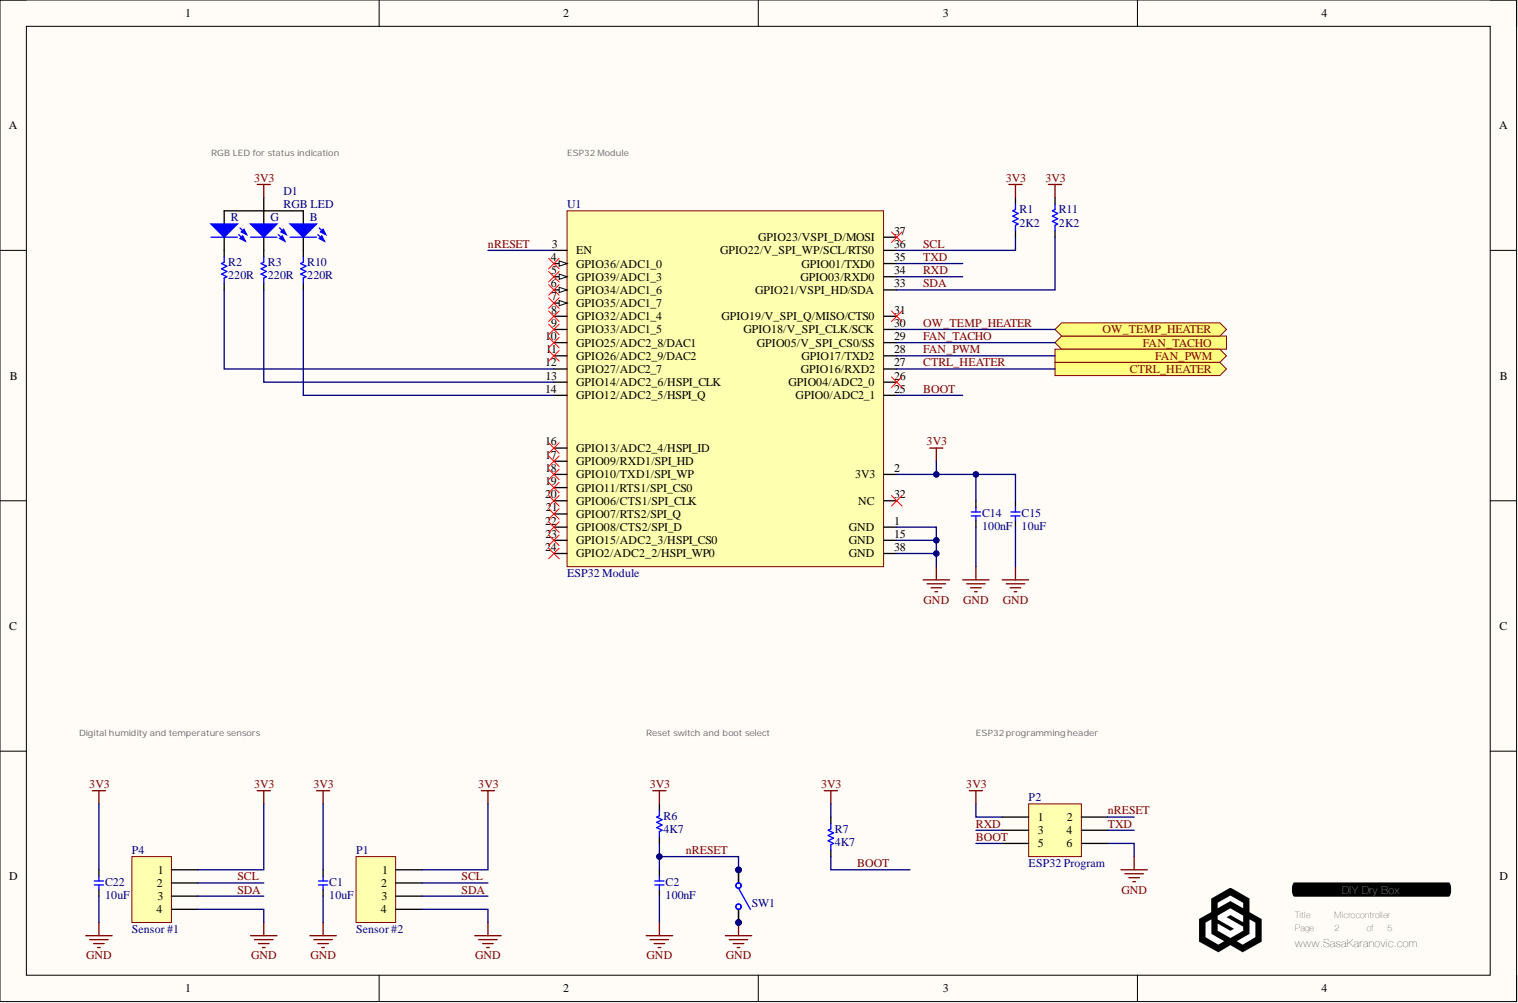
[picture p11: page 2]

SCL

GPIO36/ADC1_0 4 | | TXD RXD SDA

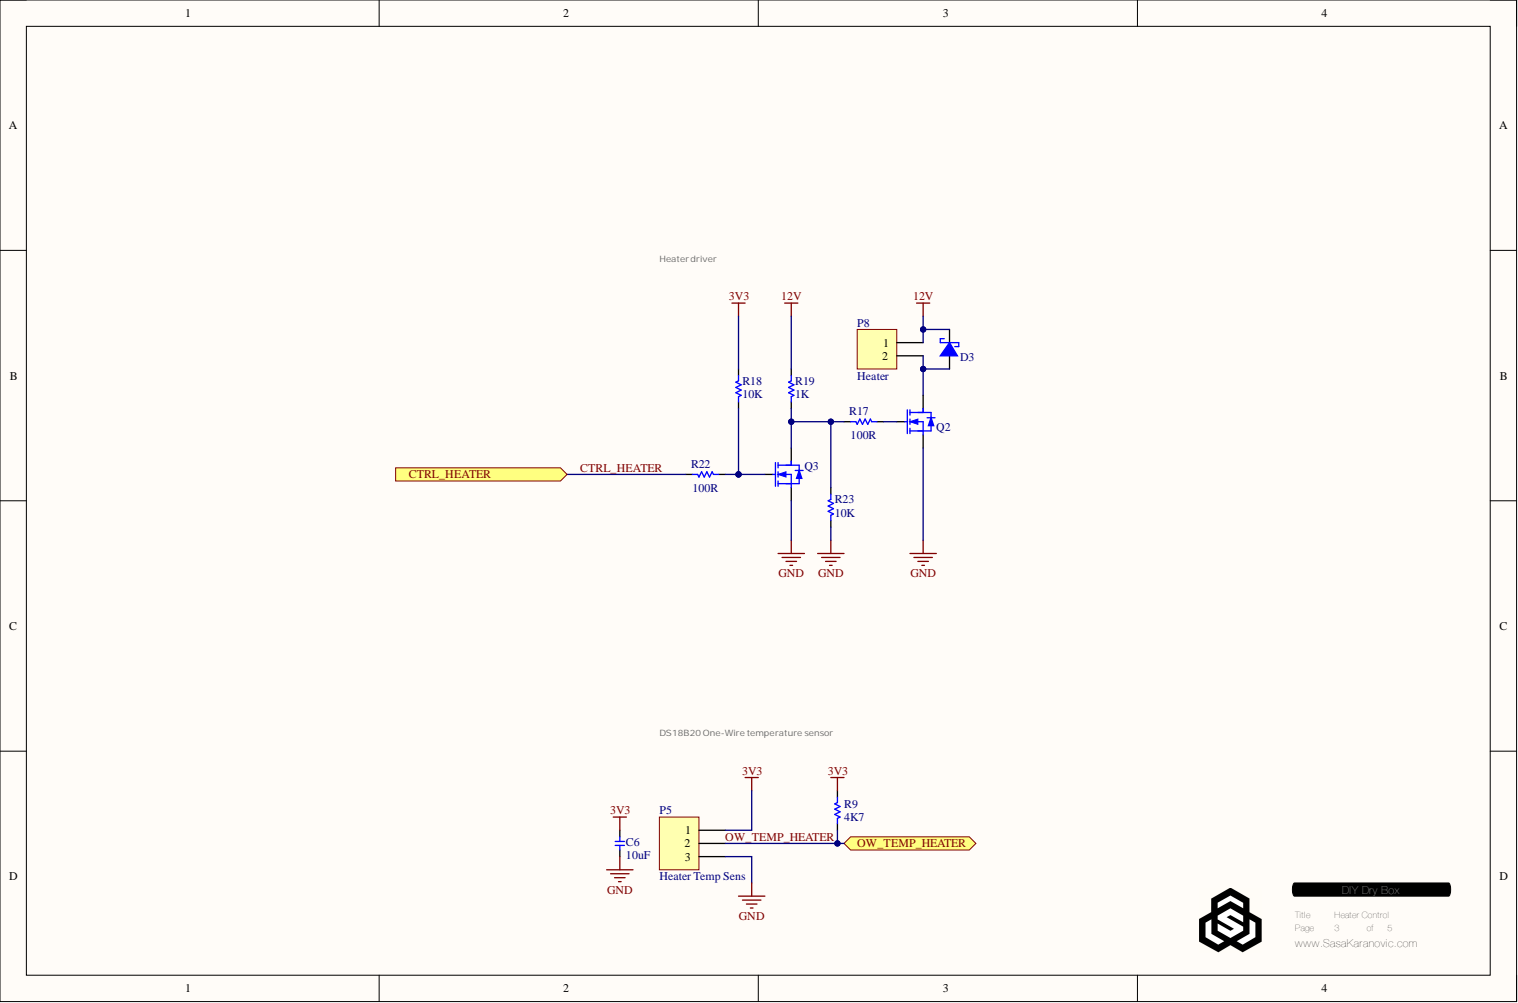
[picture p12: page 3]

DS18B20 One-Wire temperature sensor

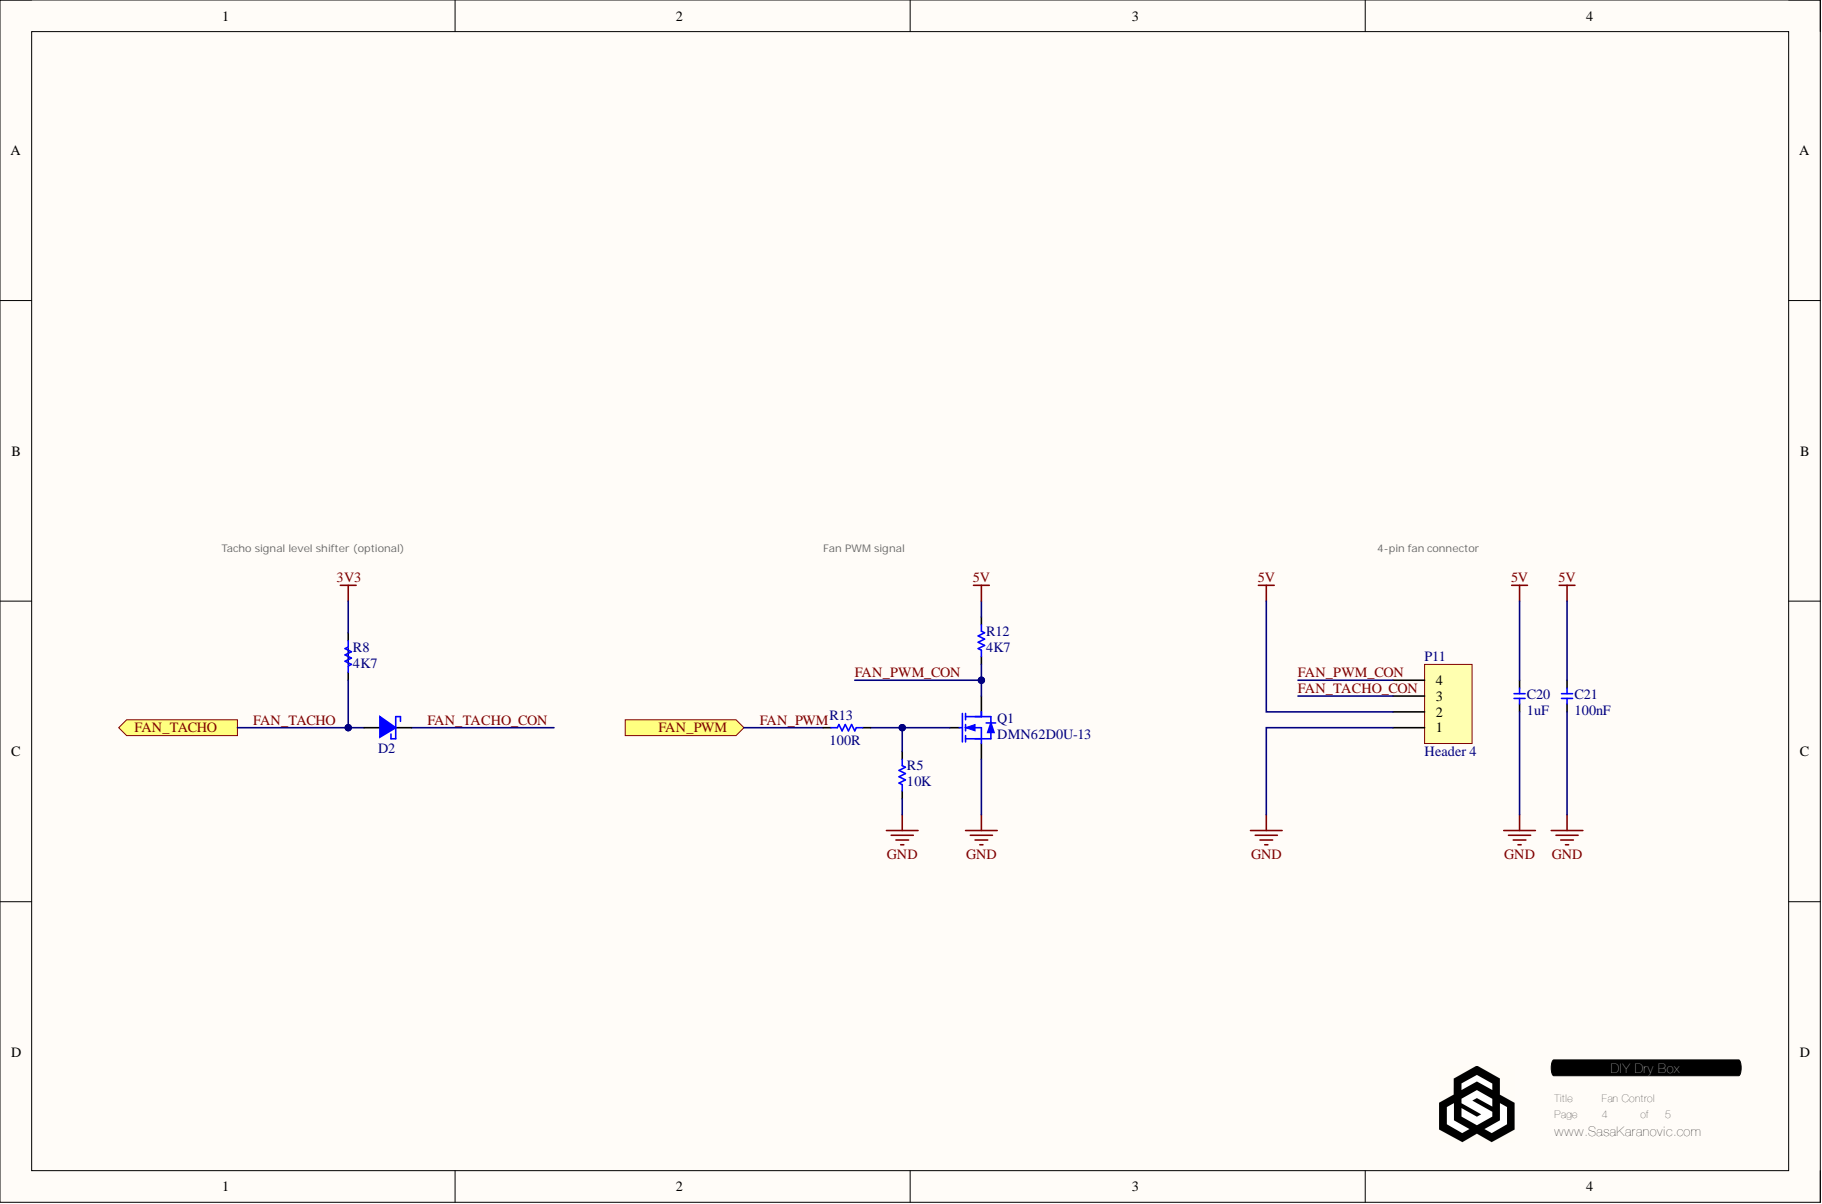
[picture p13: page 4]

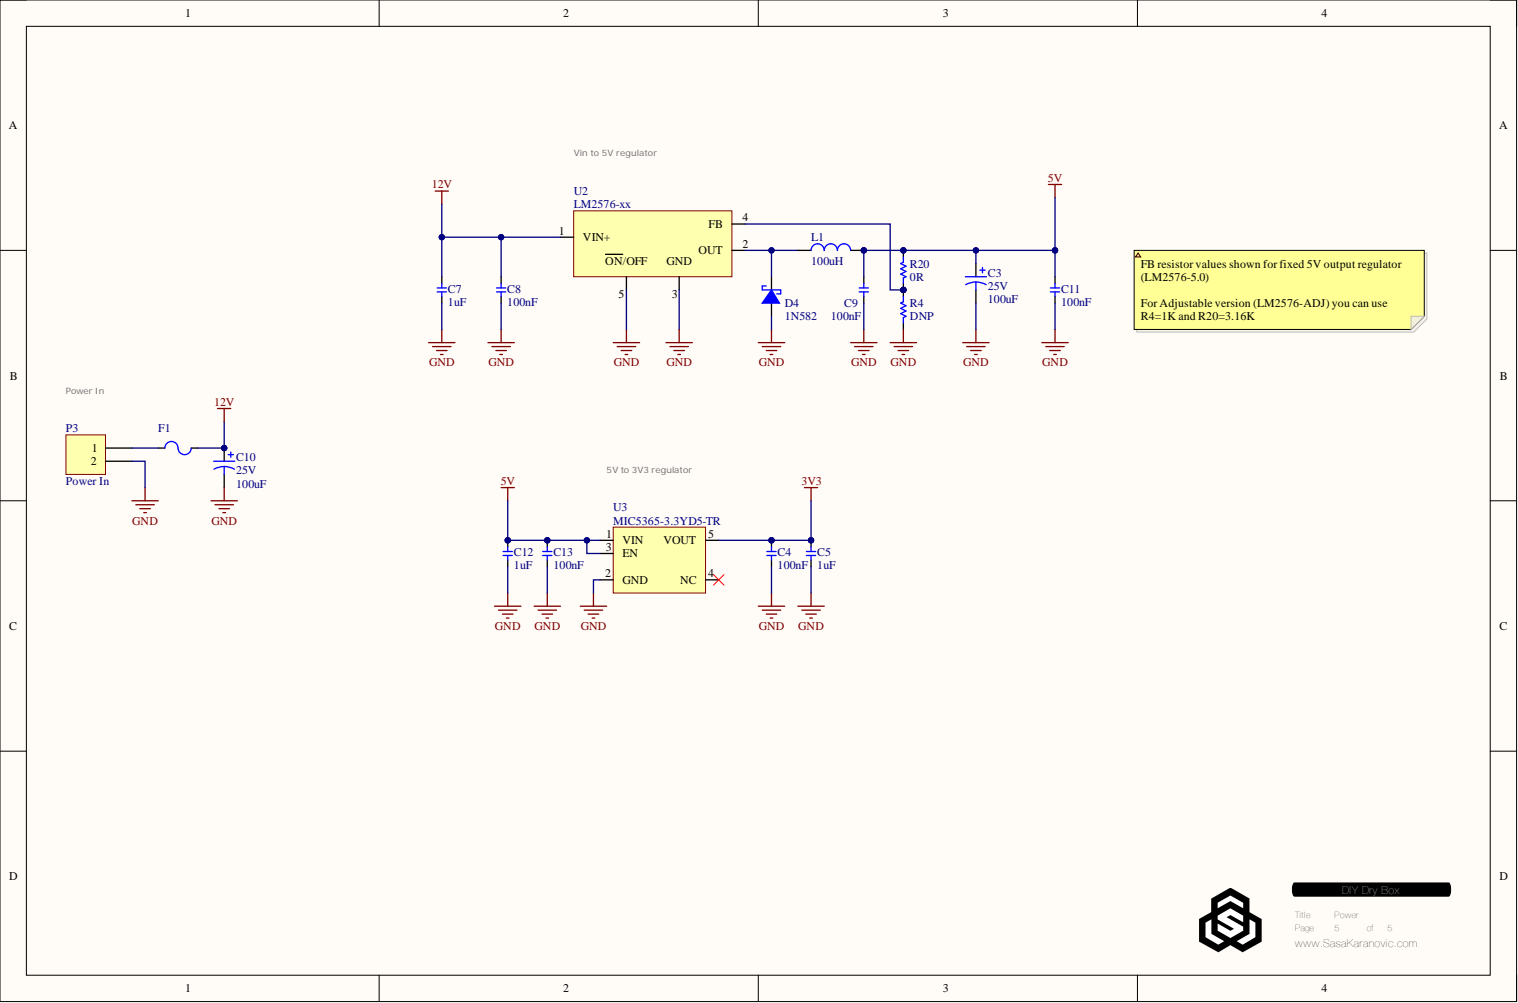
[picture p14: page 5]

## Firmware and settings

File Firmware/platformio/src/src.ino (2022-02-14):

#include "Adafruit_SHT31.h"
#include "Adafruit_Si7021.h"
#include "ESPAsyncWebServer.h"
#include "SPIFFS.h"
#include "WiFi.h"
#include <DallasTemperature.h>
#include <ESPmDNS.h>
#include <OneWire.h>
#include <Wire.h>
// Local import
#include "config.h"
#include "wifi_credentials.h"

OneWire oneWire(PIN_ONE_WIRE_BUS);
DallasTemperature oneWireSensors(&oneWire);
DeviceAddress heaterSensor;

AsyncWebServer server(80);
int WiFi_status = WL_IDLE_STATUS;

Adafruit_SHT31 temp_sensor_in = Adafruit_SHT31();
Adafruit_Si7021 temp_sensor_out = Adafruit_Si7021();

float temperature_samples_in[PID_SAMPLES] = {0};
float temperature_samples_heater[PID_SAMPLES] = {0};
uint8_t ts_pos = 0;
float target_temperature_in = 0.0;
float max_temperature_heater = 0.0;
float target_fan_percent = 10.0;
uint8_t box_status = 0;
float temperature_in = 0;
float temperature_out = 0;
float temperature_heater = 0;
float humidity_in = 0;
uint8_t fan_duty = 0;
uint8_t humidity_out = 0;
unsigned long wifi_tick_previous = 0;
unsigned long pid_first_millis = 0;
unsigned long pid_last_millis = 0;

void setup()
{
    Serial.begin(115200);
    Serial.println("Setting up GPIO");
    pinMode(PIN_HEATER_CTL, OUTPUT);
    pinMode(PIN_FAN_PWM, OUTPUT);

    pinMode(PIN_LED_RED, OUTPUT);
    pinMode(PIN_LED_GREEN, OUTPUT);
    pinMode(PIN_LED_BLUE, OUTPUT);

    LED_OFF(PIN_LED_RED);
    LED_OFF(PIN_LED_GREEN);
    LED_ON(PIN_LED_BLUE);

    // Heater PWM -- Make sure heater is initially OFF
    ledcSetup(PWM_CH_HEATER, PWM_FREQ_HEATER, PWM_RESOLUTION);
    ledcAttachPin(PIN_HEATER_CTL, PWM_CH_HEATER);
    ledcWrite(PWM_CH_HEATER, HEATER_PWM_OFF);

    // FAN PW -- Make sure FAN PWM is set to maximum (fan OFF)
    ledcSetup(PWM_CH_FAN, PWM_FREQ_FAN, PWM_RESOLUTION);
    ledcAttachPin(PIN_FAN_PWM, PWM_CH_FAN);
    ledcWrite(PWM_CH_FAN, PWM_MAX_VALUE);

    // Setup temperature and humidity oneWireSensors
    if (!temp_sensor_out.begin())
    {
        Serial.println("Can't find Si7021 sensor! (out sensor)");
        LED_ALL_OFF();
        while (1)
        {
            LED_ON(PIN_LED_BLUE);
            delay(250);
            LED_OFF(PIN_LED_BLUE);
            delay(250);
        }
    }

    Wire.setClock(10000);
    if (!temp_sensor_in.begin(0x44))
    {
        Serial.println("Can't find SHT31! (in sensor)");
        LED_ALL_OFF();
        while (1)
        {
            LED_ON(PIN_LED_GREEN);
            delay(250);
            LED_OFF(PIN_LED_GREEN);
            delay(250);
        }
    }

    oneWireSensors.begin();
    if (!oneWireSensors.getAddress(heaterSensor, 0))
    {
        Serial.println("Unable to find address for Device 0 (heater sensor)");
        while (1)
        {
            LED_ON(PIN_LED_RED);
            delay(250);
            LED_OFF(PIN_LED_RED);
            delay(250);
        }
    }

    // set the resolution to 9 bit (Each Dallas/Maxim device is capable of
    // several different resolutions)
    oneWireSensors.setResolution(heaterSensor, TEMPERATURE_PRECISION);

#if DEF_USE_WEB
    delay(1000);

    // Connect to WiFi
    Serial.print("Connecting to SSID: ");
    Serial.println(ssid);
    while (WiFi_status != WL_CONNECTED)
    {
        Serial.print(".");
        WiFi_status = WiFi.begin(ssid, password);
        // wait 5 seconds and check again
        delay(5000);
    }
    Serial.println("");

    if (!MDNS.begin(MDNS_NAME))
    {
        Serial.println("Error starting mDNS");
    }
    else
    {
        Serial.println((String) "mDNS http://" + MDNS_NAME + ".local");
    }

    // Initialize SPIFFS
    if (!SPIFFS.begin(true))
    {
        Serial.println("An Error has occurred while mounting SPIFFS");
        while (1)
        {
            LED_ON(PIN_LED_RED);
            delay(500);
            LED_OFF(PIN_LED_RED);
            delay(500);
        }
    }

    Serial.print("WiFi IP: ");
    Serial.println(WiFi.localIP());

    setupWebServer();
    server.begin();

#if DEF_DEUG_SPIFFS
    debug_spiffs_files();
#endif

#endif
    Serial.println("Ready to go.");
    LED_OFF(PIN_LED_BLUE);
}

//
// 	** Main loop **
//
void loop()
{
    // Sample temperature and humidity from all available sensors
    if (!readHeaterTemperature(&temperature_heater))
    {
        // Handle heater sensor error
        Serial.println("Failed to read heater temperature!");
    }
    sample_sens_in_and_out();

// Debug
#if DEF_DEBUG_HETER_SAMPLES
    Serial.println((String)temperature_in + "\t" + temperature_heater + "\t" +
                   target_temperature_in);
#endif

    // Check if we have WiFi connection, if not try to reconnect
    check_wifi_connection();

    // Dry box is active
    if (box_status)
    {
        LED_ON(LED_STATUS_HEATER);
        // Sample temperature values
        if (sample_temperatures(temperature_in, temperature_heater))
        {
            // Recalculate PWM value for the heater
            heater_recalc_pwm();
        }
    }
    // Drybox is off. Turn/Keep off the heater
    else
    {
        LED_OFF(LED_STATUS_HEATER);
        set_heater_duty(HEATER_DUTY_OFF);
    }
}

void debug_spiffs_files(void)
{
    File root = SPIFFS.open("/");
    File file = root.openNextFile();

    while (file)
    {
        Serial.print("FILE: ");
        Serial.println(file.name());
        file = root.openNextFile();
    }
}

void sample_sens_in_and_out(void)
{
    float tmp_temp = 0.0;
    float tmp_humid = 0.0;
    uint8_t i = 5;

    while (i--)
    {
        tmp_temp = temp_sensor_out.readTemperature();
        // delay(5);
        tmp_humid = temp_sensor_out.readHumidity();
        if (!isnan(tmp_temp) && !isnan(tmp_humid))
        {
            break;
        }
        delay(50);
    }

    // Make sure final values are valid
    if (!isnan(tmp_temp) && !isnan(tmp_humid))
    {
        temperature_out = tmp_temp;
        humidity_out = tmp_humid;
#if DEF_DEBUG_SENSOR_SAMPLES
        Serial.println((String) "TempOut:" + temperature_out +
                       " - HumidOut:" + humidity_out);
#endif
    }
    // Otherwise we have a problem
    else
    {
        Serial.println("Out sensor: I2C error!");
    }

    // Read SHT temperature and humidity
    while (i--)
    {
        tmp_temp = temp_sensor_in.readTemperature();
        // delay(5);
        tmp_humid = temp_sensor_in.readHumidity();
        if (!isnan(tmp_temp) && !isnan(tmp_humid))
        {
            break;
        }
        delay(50);
    }

    // Make sure final values are valid
    if (!isnan(tmp_temp) && !isnan(tmp_humid))
    {
        temperature_in = tmp_temp;
        humidity_in = tmp_humid;
#if DEF_DEBUG_SENSOR_SAMPLES
        Serial.println((String) "TempIn:" + temperature_in +
                       " - HumidIn:" + humidity_in);
#endif
    }
    // Otherwise we have a problem
    else
    {
        Serial.println("In sensor: I2C error!");
    }
}

bool readHeaterTemperature(float *fpTemp)
{
    float tempC;
    uint8_t i = 5;

    while (i--)
    {
        oneWireSensors.requestTemperatures();
        delay(20);
        tempC = oneWireSensors.getTempC(heaterSensor);
        if (tempC != DEVICE_DISCONNECTED_C)
        {
            *fpTemp = tempC;
#if DEF_DEBUG_SENSOR_SAMPLES
            Serial.print("Temp C: ");
            Serial.println(tempC);
#endif
            return true;
        }
        else
        {
#if DEF_DEBUG_SENSOR_SAMPLES
            Serial.println((String) "Heater sensor fault: " + tempC);
#endif
        }
        delay(20);
    }

    return false;
}

void set_fan_duty(uint8_t duty)
{
    if (duty > 100)
    {
        duty = 100;
    }

    fan_duty = duty;
    uint32_t pwm_raw_fan = ((PWM_MAX_VALUE * (100 - duty)) / 100.0);
#if DEF_DEBUG_PWM_VALUES
    Serial.println((String) "Setting fan to " + pwm_raw_fan);
#endif
    ledcWrite(PWM_CH_FAN, pwm_raw_fan);
}

void set_heater_duty(uint8_t duty)
{
    uint32_t pwm_raw_heater = 0;
    if (duty > 100)
    {
        duty = 100;
    }

    pwm_raw_heater = ((PWM_MAX_VALUE * duty) / 100.0);

#if DEF_DEBUG_PWM_VALUES
    Serial.println((String) "Setting heater duty " + duty + "%");
#endif
    set_heater_pwm(pwm_raw_heater);
}

void set_heater_pwm(uint32_t pwm)
{
    if (pwm > PWM_MAX_VALUE)
    {
        pwm = PWM_MAX_VALUE;
    }

#if PWM_HEATER_INVERT_VALUES
    pwm = PWM_MAX_VALUE - pwm;
#endif
#if DEF_DEBUG_PWM_VALUES
    Serial.println((String) "set_heater_duty: " + pwm + "/" + PWM_MAX_VALUE);
#endif
    ledcWrite(PWM_CH_HEATER, pwm);
}

bool sample_temperatures(float in, float heater)
{
    temperature_samples_in[ts_pos] = in;
    temperature_samples_heater[ts_pos] = heater;

    ts_pos++;
    if (ts_pos == 0)
    {
        // Record milliseconds of our first sample
        pid_first_millis = millis();
    }
    if (ts_pos >= PID_SAMPLES)
    {
        pid_last_millis = millis();
        ts_pos = 0;
        return true;
    }
    else
    {
        return false;
    }
}

void heater_recalc_pwm(void)
{
    // We are using a simple PID-like control loop to calculate PWM value for a
    // heater Heater is heating up our box to a target temperature and keeping
    // it steady after/if that temperature is reached. At the same time we have
    // to ensure heater does not go beyond our "safe" temperature and start
    // damaging itself/fillament/cables/enclosure etc.
    //
    // As a simple solution, we will use the following flow
    // 1. Check if heater temperature is higher or equal to the maximum set
    // heater temperature
    // 		- if True, use heater max temperature as the target for our PID
    // controller
    // 		- if False, use enclosure maximum temperature as the target for
    // our PID controller

    float average = 0;
    float pid_del_p;
    float pid_del_i;
    float pid_del_d;
    int32_t pid_val_p;
    int32_t pid_val_i;
    int32_t pid_val_d;
    int32_t pwm_val;
    float pid_target_temperature = 0.0;
    float pid_temperature = 0.0;
    float pid_temperature_previous = 0.0;
    unsigned long pid_time_diff;

    // Make sure values are valid
    if (isnan(temperature_heater))
    {
        Serial.println("Invalid temperature values");
        Serial.println((String) "temp_heater:" + temperature_heater);
        Serial.println((String) "target_temperature_in:" +
                       target_temperature_in);
        set_heater_duty(HEATER_DUTY_OFF);
        return;
    }

    // Inside temperature has NOT reached the target temperature
    // However, heater temperature is approaching it's maximum allowed
    // temperature. Then, regulate heater max temperature
    if ((temperature_heater >= (max_temperature_heater - PID_TEMP_PROXIMITY)) &&
        (temperature_in < target_temperature_in))
    {
        Serial.println("Using HEATER temperature as target.");
        for (uint8_t i = 0; i < PID_SAMPLES; i++)
        {
            average += temperature_samples_heater[i];
        }
        average = average / PID_SAMPLES;

        pid_target_temperature = max_temperature_heater;
        pid_temperature = temperature_heater;
        pid_temperature_previous = temperature_samples_heater[PID_SAMPLES - 1];
    }
    // Heater is not close to it's maximum allowed temperature
    // Or, inside temperature has already reached the target value
    else
    {
        Serial.println("Using IN temperature as target.");
        for (uint8_t i = 0; i < PID_SAMPLES; i++)
        {
            average += temperature_samples_in[i];
        }
        average = average / PID_SAMPLES;

        pid_target_temperature = target_temperature_in;
        pid_temperature = temperature_in;
        pid_temperature_previous = temperature_samples_in[PID_SAMPLES - 1];
    }

    // P
    pid_del_p = pid_target_temperature - pid_temperature;
    pid_val_p = (uint32_t)(pid_del_p)*PID_KP;

    // I
    pid_del_i = pid_target_temperature - average;
    pid_val_i = (uint32_t)(pid_del_i)*PID_KI;

    // D
    pid_del_d = pid_target_temperature - pid_temperature_previous;
    pid_time_diff = pid_last_millis - pid_first_millis;
    if (pid_time_diff > 0)
    {
        pid_val_d = (uint32_t)(pid_del_d) / pid_time_diff;
        pid_val_d = (uint32_t)(pid_val_d)*PID_KD;
    }
    else
    {
        pid_val_d = 0;
    }

    // P + I + D
    pwm_val = pid_val_p + pid_val_i + pid_val_d;

#if DEF_DEBUG_PID
    Serial.println((String) "Pd: " + pid_del_p);
    Serial.println((String) "Pv: " + pid_val_p);
    // Serial.println((String)"Ia: "+ sum);
    Serial.println((String) "Id: " + pid_del_i);
    Serial.println((String) "Iv: " + pid_val_i);
    Serial.println((String) "Dd: " + pid_del_d);
    Serial.println((String) "Dv: " + pid_val_d);
    Serial.println((String) "Calc PWM val: " + pwm_val);
#endif

    if (pwm_val > PWM_MAX_VALUE)
    {
        pwm_val = PWM_MAX_VALUE;
    }
    else if (pwm_val < 0)
    {
        pwm_val = 0;
    }

#if DEF_DEBUG_PID
    Serial.println((String) "New PWM val: " + pwm_val);
#endif
    set_heater_pwm(pwm_val);
}

void setupWebServer(void)
{
    server.onNotFound([](AsyncWebServerRequest *request) {
        Serial.println("404:");
        Serial.println(request->url());
        request->send(404);
    });

    // // send a file when /index is requested
    server.on("/index.html", HTTP_ANY, [](AsyncWebServerRequest *request) {
        request->send(SPIFFS, "/index.html");
    });

    // send a file when /index is requested
    server.on("/", HTTP_ANY, [](AsyncWebServerRequest *request) {
        request->send(SPIFFS, "/index.html");
    });

    server.serveStatic("/img/", SPIFFS, "/img/");
    server.serveStatic("/css/", SPIFFS, "/css/");
    server.serveStatic("/js/", SPIFFS, "/js/");
    server.serveStatic("/webfonts/", SPIFFS, "/webfonts/");

    // Get dry box status
    server.on("/status", HTTP_GET, [](AsyncWebServerRequest *request) {
        char buff[200] = {0};
        int len;
        len =
            snprintf(buff, 200,
                     "{\"status\":%d, \"target_temp_in\":%f, "
                     "\"max_temp_heater\":%f, "
                     "\"temp_in\":%f, \"temp_heater\":%f, \"humid_in\":%f, "
                     "\"fan_speed\":%d, \"temp_out\":%f, \"humid_out\":%d}",
                     box_status, target_temperature_in, max_temperature_heater,
                     temperature_in, temperature_heater, humidity_in, fan_duty,
                     temperature_out, humidity_out);

        if (len)
        {
            request->send(200, "text/plain", buff);
        }
        else
        {
            request->send(500, "text/plain",
                          "{\"status\": \"Internal server error\"}");
        }
    });

    // Turn OFF dry box
    server.on("/off", HTTP_GET, [](AsyncWebServerRequest *request) {
        box_status = 0;
        set_fan_duty(0);
        set_heater_duty(HEATER_DUTY_OFF);
        target_temperature_in = 0;
        max_temperature_heater = 0;
        request->send(200, "text/plain", "{\"status\": \"OK\"}");
    });

    // Turn ON dry box and set target temperature, max heater temperature and fan speed
    server.on("/set", HTTP_GET, [](AsyncWebServerRequest *request) {
        // Check if temperature, heater temperature and fan speed arguments are present
        if (request->hasParam("temperature") && request->hasParam("heater") &&
            request->hasParam("fanspeed"))
        {
            String str_temperature;
            String str_heater;
            String str_fanspeed;
            int32_t temperature = 0;
            int32_t heater = 0;
            int32_t fanspeed = 0;

            str_temperature = request->getParam("temperature")->value();
            temperature = str_temperature.toInt();

            str_heater = request->getParam("heater")->value();
            heater = str_heater.toInt();

            str_fanspeed = request->getParam("fanspeed")->value();
            fanspeed = str_fanspeed.toInt();

#if DEF_DEUG_WEB_API
            Serial.println((String) "Target temp: " + temperature +
                           "C Heater: " + heater + "C Fan Speed: " + fanspeed);
#endif

            // Check drybox temperature and heater temperature limit
            if ( (temperature <= LIMIT_TEMP_IN_MAX) && (heater <= LIMIT_TEMP_HEATER_MAX) )
            {
                target_temperature_in = temperature;
                max_temperature_heater = heater;
                set_fan_duty(fanspeed);
                box_status = 1;
                request->send(200, "text/plain", "{\"status\": \"OK\"}");
                return;
            }
            // If either of them are out of range, return bad request status
            else
            {
                request->send(400, "text/plain", "{\"status\": \"Bad request. Limit error!\"}");
                return;
            }

        }
        // Not all arguments are present in the request
        else
        {
            request->send(400, "text/plain", "{\"status\": \"Bad request\"}");
            return;
        }
    });
}

void check_wifi_connection(void)
{
    unsigned long currentMillis = millis();

    // Check WiFi status every WIFI_CHECK_CONNECTION_MS miliseconds
    if ((currentMillis - wifi_tick_previous) >= WIFI_CHECK_CONNECTION_MS)
    {
        if (WiFi.status() == WL_CONNECTED)
        {
            LED_ON(LED_STATUS_WIFI);
            LED_OFF(PIN_LED_BLUE);
        }
        else
        {
            LED_OFF(LED_STATUS_WIFI);
            LED_ON(PIN_LED_BLUE);
            Serial.println("Reconnecting to WiFi...");
            WiFi.disconnect();
            WiFi.reconnect();
        }

        wifi_tick_previous = currentMillis;
    }
}

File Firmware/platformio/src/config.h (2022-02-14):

#ifndef _DIY_DRYBOX_CFG_H_
#define _DIY_DRYBOX_CFG_H_
// clang-format off
#define MDNS_NAME                   "drybox"
#define PIN_ONE_WIRE_BUS            18
#define PIN_HEATER_CTL              16
#define PIN_FAN_PWM                 17
#define PIN_FAN_TACHO               5
#define PIN_LED_RED                 27
#define PIN_LED_GREEN               14
#define PIN_LED_BLUE                12
#define LED_ON(x)                   do{digitalWrite(x, LOW);}while(0)
#define LED_OFF(x)                  do{digitalWrite(x, HIGH);}while(0)

#define LED_ALL_OFF()               do{digitalWrite(PIN_LED_RED, HIGH);\
                                        digitalWrite(PIN_LED_GREEN, HIGH);\
                                        digitalWrite(PIN_LED_BLUE, HIGH); }while(0)
#define LED_ALL_ON()                do{digitalWrite(PIN_LED_RED, LOW);\
                                        digitalWrite(PIN_LED_GREEN, LOW);\
                                        digitalWrite(PIN_LED_BLUE, LOW); }while(0)
#define LED_STATUS_WIFI             PIN_LED_GREEN
#define LED_STATUS_HEATER           PIN_LED_RED
#define PID_SAMPLES                 5
#define PID_TEMP_PROXIMITY          5
#define PID_KP                      65
#define PID_KI                      81
#define PID_KD                      50

#define PWM_HEATER_INVERT_VALUES    1
#define PWM_FREQ_HEATER             500
#define PWM_FREQ_FAN                25000
#define PWM_RESOLUTION              10
#define PWM_MAX_VALUE               1024L
#define HEATER_DUTY_OFF             0
#define HEATER_PWM_OFF              PWM_MAX_VALUE
#define PWM_CH_HEATER               0
#define PWM_CH_FAN                  2

#define TEMPERATURE_PRECISION       10
#define LIMIT_TEMP_IN_MIN           20
#define LIMIT_TEMP_IN_MAX           70
#define LIMIT_TEMP_HEATER_MIN       20
#define LIMIT_TEMP_HEATER_MAX       75
#define LIMIT_FAN_SPEED_MIN         0
#define LIMIT_FAN_SPEED_MAX         100

#define WIFI_CHECK_CONNECTION_MS    10000

#define DEF_USE_WEB                 1
#define DEF_DEBUG_CALIBRATE_ADC     0
#define DEF_DEBUG_PID               0
#define DEF_DEBUG_HETER_SAMPLES     0
#define DEF_DEBUG_SENSOR_SAMPLES    0
#define DEF_DEBUG_PWM_VALUES        0
#define DEF_DEUG_SPIFFS             0

// clang-format on
#endif

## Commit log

2022-02-14 Initial commit after public rebase.
    [01_Top.SchDoc, 02_Microcontroller.SchDoc, 03_Heater_Control.SchDoc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]
2022-02-18 Adding desiccant and fan holder STL files.
    [Desiccant_Cap_PLA_or_PETG.stl, Desiccant_Holder_PLA_or_PETG.stl, FanHolder_PLA_or_PETG.stl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]
2023-04-29 Correcting U3 part number. Updating release files.
    [05_Power.SchDoc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]
2026-05-19 Fixing BoM typo.
